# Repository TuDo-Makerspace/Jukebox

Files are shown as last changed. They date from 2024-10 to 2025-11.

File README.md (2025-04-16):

# Jukebox

This repository contains everything related to our sacred Jukebox. For more information, please refer to one of the following sections:

- [Usage](https://tudo-makerspace.github.io/Jukebox/Docs/Usage.html)
- [Hardware Documentation](https://tudo-makerspace.github.io/Jukebox/Docs/Hardware.html)
- [Software Documentation]() TODO

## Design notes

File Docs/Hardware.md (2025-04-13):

# Hardware

## Jukebox

The original jukebox used in our project is an [NSM Satellite 200](https://www.jukebox-world.de/Forum/Archiv/NSM/NSMSatellite200.htm), likely produced sometime in the late 1980s.

In this document we will only cover the hardware modifications made for our project. For detailed information on the jukebox's original hardware and specifications, please consult the following resources:

- [NSM Satellite 200 on Jukebox-World.de](https://www.jukebox-world.de/Forum/Archiv/NSM/NSMSatellite200.htm)
- [NSM Satellite 200 at Propstore Auction](https://propstoreauction.com/lot-details/index/catalog/359/lot/119259)
- [NSM Jukebox Image Archive on Jukebox-World.de](https://www.jukebox-world.de/Forum/Archiv/NSM/NSM-Bilder-Uebersicht.htm)

## Modifications

Most original components of the jukebox were removed and replaced with modern hardware. The primary modifications include:

- Logic and Playback: The primary logic and audio playback are now managed by a Raspberry Pi. *(TODO: Specify Raspberry Pi model)*
- Speakers: The Original speakers have been replaced. *(TODO: Document exact speaker model/specifications)*
- Audio Processing and Amplification: Audio output is managed by a [WONDOM APM2 DSP Board](https://store.sure-electronics.com/product/AA-AP23122) in combination with two amplifier boards. *(TODO: Specify amplifier board models)*
- Volume Control: The volume adjustment buttons located at the back of the jukebox are directly wired to the DSP board.
- Lighting: The original lighting controller was replaced by a custom lamp driver board which can be driven directly from the Raspberry Pi.
- Keypad Interface: A custom keypad decoder circuit was developed, allowing the Raspberry Pi to interpret user input from the original jukebox keypad.

### Power Supply

The jukebox utilizes two 12V power supplies and two 5V USB adapters to power its components:

- Audio Components: One low-noise 12V power supply provides clean, stable power specifically for audio components.
- Lamps: A separate 12V power supply independently powers the lamps.
- RPi and DSP Board: Two dedicated 5V USB adapters supply power to the Raspberry Pi and the DSP board.

All power supplies are connected to single power strip.

*(TODO: Specify exact power supply models/ratings)*

## Components

The following picture highlights all the components built into the jukebox:

TODO Add picture

Here's the respective block diagram:

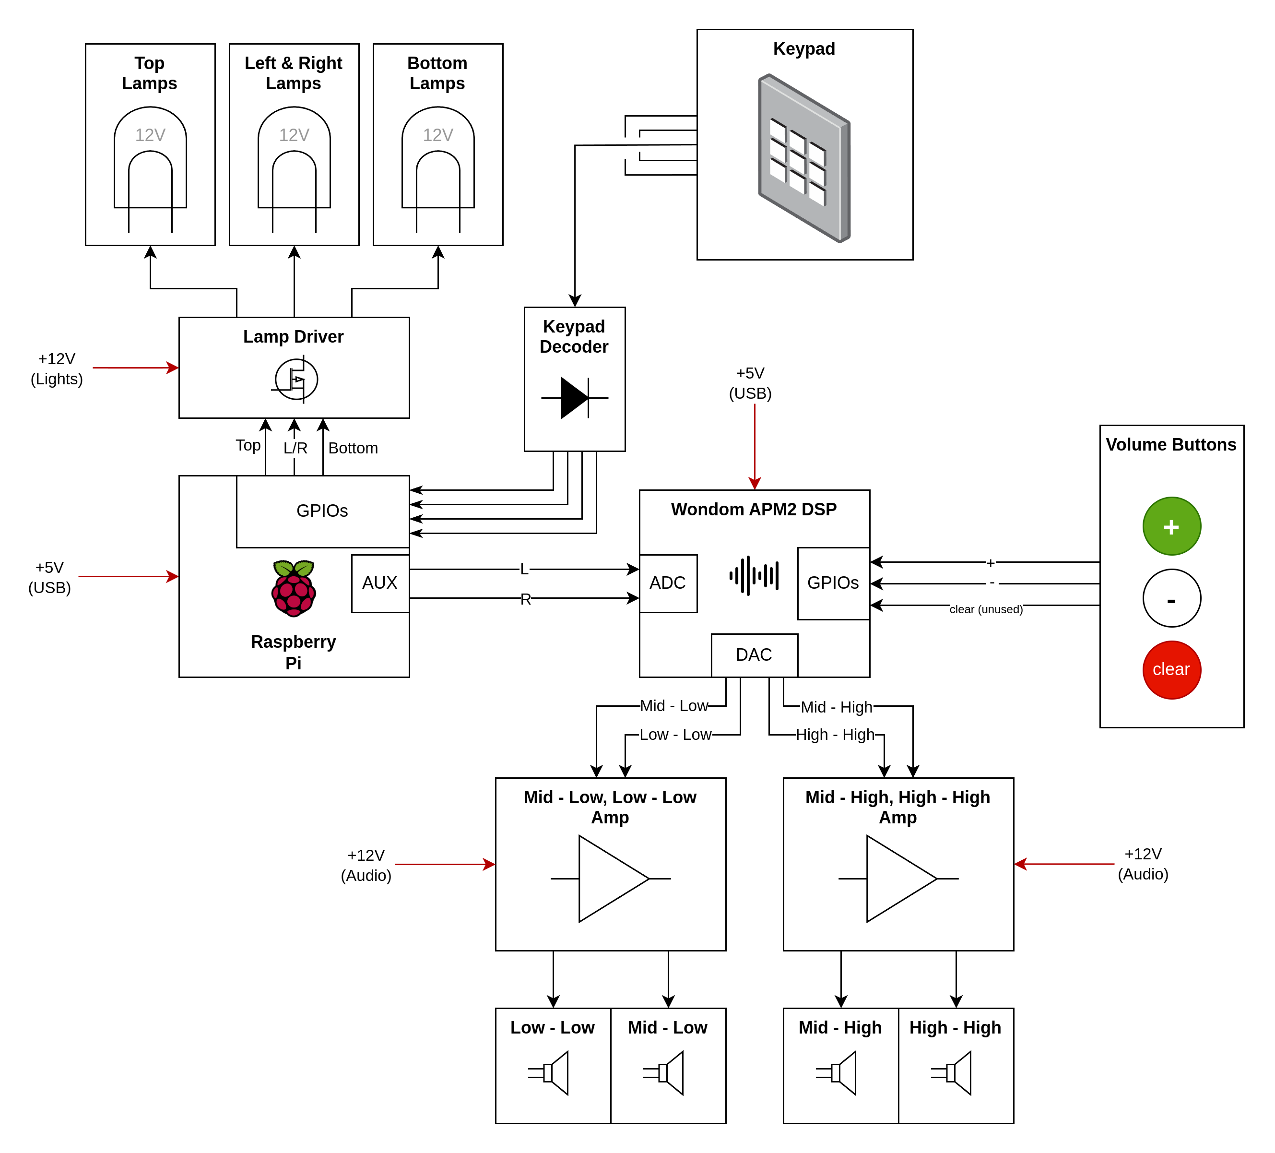
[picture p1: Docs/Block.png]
Block Diagram


### Raspberry Pi

The Raspberry Pi serves as the primary control unit for the jukebox, managing all logical operations and handling song playback. Detailed information about the software running on the Pi can be found in the [software documentation](https://tudo-makerspace.github.io/Jukebox/Docs/Software.html).

To interface with other components, a custom perfboard has been created, which plugs directly into the Raspberry Pi's GPIO pins. This perfboard provides connections to the lamp driver. It also contains the keypad decoder circuit (refer to the Keypad section for more details) along with a connection to the Keypad PCB itself.

Audio output from the Raspberry Pi is routed via its built-in 3.5mm audio jack, which connects directly to the DSP board. Initially, an attempt was made to utilize the I²S interface for improved audio fidelity; however, due to reliability issues arising from the Raspberry Pi's lack of a dedicated master clock, this approach was abandoned. Consequently, the perfboard contains several unused wires that were intended for I²S connections.

Power to the Raspberry Pi is supplied by a dedicated 5V USB adapter through its micro USB port.

### Lamp Driver

The jukebox uses [standard 12V T10 lamps](https://www.amazon.de/dp/B0CBKYPM57?ref_=ppx_hzsearch_conn_dt_b_fed_asin_title_1) distributed across three independently controllable segments:

- Top
- Left & Right (wired together)
- Bottom

To control these segments, a custom lamp driver board was designed to convert the Raspberry Pi’s 3.3V GPIO outputs to 12V control signals. The KiCAD design files are available [here](https://github.com/TuDo-Makerspace/Jukebox/tree/main/Lamps).

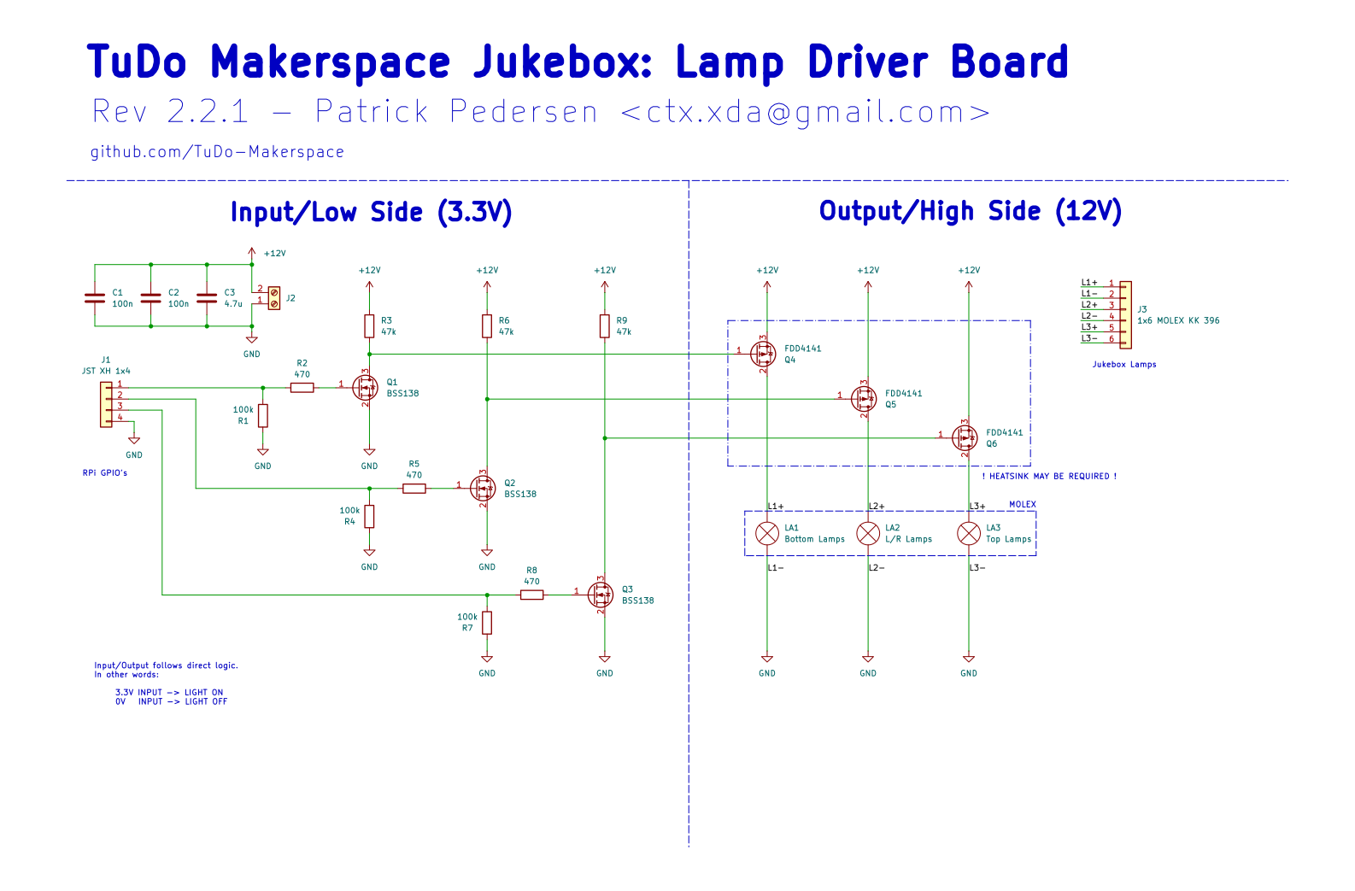
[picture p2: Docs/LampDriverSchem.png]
Lamp Driver Schematic


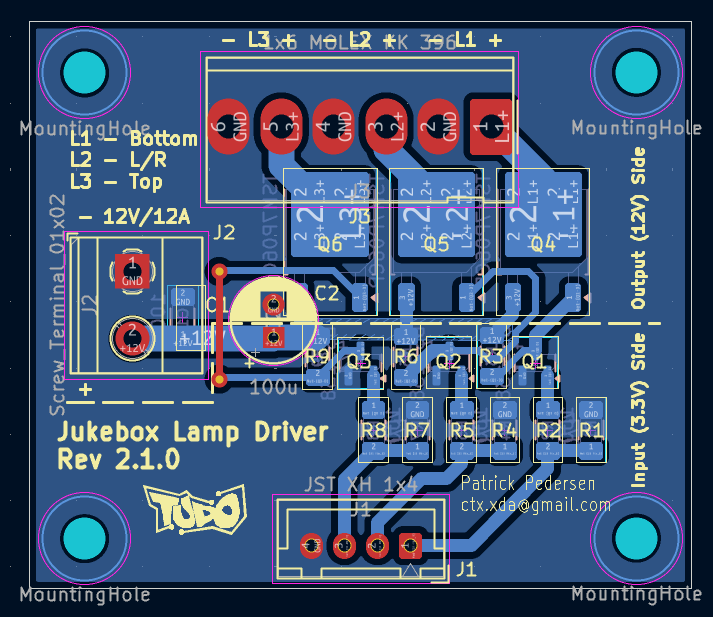
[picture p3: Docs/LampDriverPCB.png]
Lamp Driver PCB


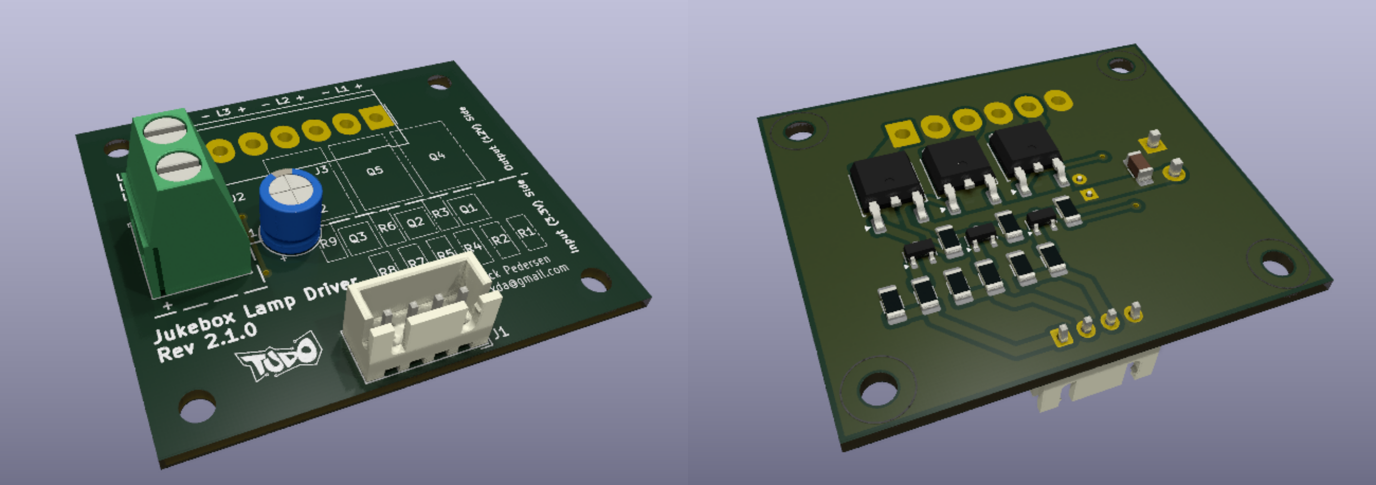
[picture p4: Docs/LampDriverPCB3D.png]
Lamp Driver PCB 3D


The lamp driver receives 12V power from the lighting power supply and connects to the Raspberry Pi via a 4-pin JST connector carrying `GND`, `Top`, `L/R`, and `Bottom` signals. Lamp outputs are routed through a 6-pin Molex connector, with each segment receiving a dedicated `+` and `-` connection. When all lamps are active, the board can draw up to 6A at 12V, with the `L/R` segment being the most power-hungry (up to 3A).

Signal amplification is handled in two stages:
1. The 3.3V GPIO signal is boosted to 12V using a BSS138 N-channel MOSFET.
2. This 12V signal is then used to switch a P-channel power MOSFET that controls the lamp segment.

In the current hardware revision, **TSM7P06CP** P-MOSFETs are used instead of the **FDD4141** parts shown in the schematic. Unfortunately, the TSM7P06CP has a significantly higher R<sub>DS(on)</sub>, which leads to heat buildup under load. Thermal testing has shown temperatures reaching up to 60°C with the current heatsink. While this remains within safe operating limits, we added a layer of Kapton tape between the heatsink and the wooden enclosure as a precaution.

**Recommendation:** For improved thermal performance, we suggest replacing the TSM7P06CP MOSFETs with FDD4141s in a future revision. This can be done either by updating the PCB layout or replacing the components on the current board.

### Keypad

TODO

### DSP

### DSP Board

The jukebox’s audio processing is handled by a [WONDOM APM2 DSP Board](https://store.sure-electronics.com/product/AA-AP23122).

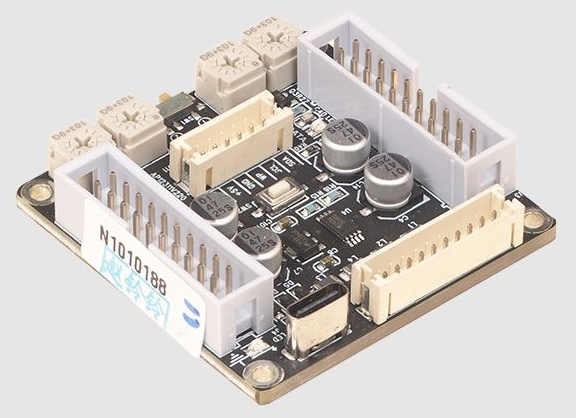
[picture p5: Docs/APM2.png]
WONDOM APM2 DSP Board


The DSP board primarily functions as a 4-way crossover, splitting the incoming audio signal into four distinct frequency bands:

- Low-Low
- Low-Mid
- High-Mid
- High-High

The board receives stereo audio input from the Raspberry Pi’s 3.5mm jack via its ADC input pins (AINL, AINR) and outputs processed audio through four DAC channels (DAC0–DAC3), which are connected to two separate amplifier boards.

The volume and clear buttons on the back of the jukebox are directly wired to the GPIO pins of the DSP board:

| Button | GPIO Pin |
| --- | --- |
| + | GPIO 10  |
| - | GPIO 11  |
| Clear  | TODO |

The volume buttons adjust the gain of the DSP, while the clear button is currently unused.

The DSP configuration is developed and uploaded using [SigmaStudio](https://www.analog.com/en/resources/evaluation-hardware-and-software/embedded-development-software/ss_sigst_02.html). The corresponding project file is available [here](https://github.com/TuDo-Makerspace/Jukebox/tree/main/Sound/DSP).

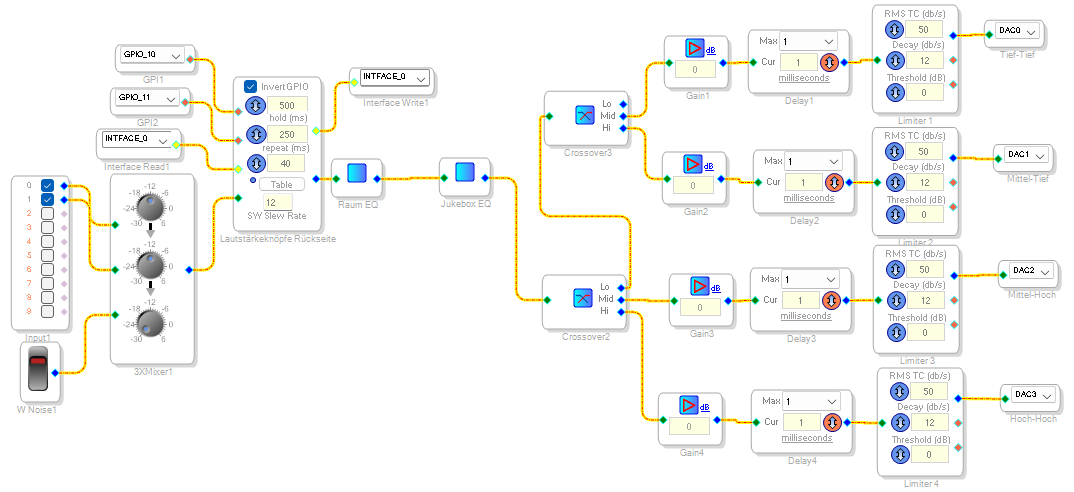
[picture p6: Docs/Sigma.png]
Sigma Studio


A dedicated USB programming board is used to upload the SigmaStudio configuration. It can be found inside the jukebox.

Further documentation and details about the DSP board, as well as how to program it, can be found in [this manual](https://files.sure-electronics.com/download/The_correspondence_of_APM2_hardware_and_DSP_program.pdf). [Video tutorials](https://www.youtube.com/watch?v=TjN1SGKeVvw) are also available.

#### Troubleshooting Tips

Here are some common frustrations we encountered while working with the DSP board:

- **USB not recognized (usb device highlighted red):**
    - Power off the DSP board and unplug the programmer
    - Unplug the programmer's USB cable
    - Replug the programmer's USB cable, check for the device to appear green in SigmaStudio
    - Plug the programmer into the DSP board
    - Power on the DSP board (That being said, it should already be powered on through the programmer at this point)

- **EEPROM programming stuck at "Start Download":**
    - Click *Link Project*
    - Click *Link Compile Connect*
    - Finally, click *Link Compile Download*
    - Try flashing the EEPROM again

#### Future Plans

We plan to measure the frequency response of the speakers to implement a tailored equalizer using the DSP board.

### Amplifier Boards

TODO

### Speakers

TODO

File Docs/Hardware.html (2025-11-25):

# Jukebox Hardware Docs

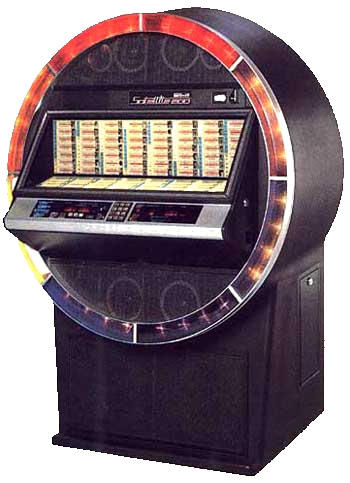
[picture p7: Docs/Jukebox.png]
Jukebox


## Jukebox

The original jukebox used in our project is an NSM Satellite 200 (https://www.jukebox-world.de/Forum/Archiv/NSM/NSMSatellite200.htm), likely produced sometime in the late 1980s.

In this document we will only cover the hardware modifications made for our project. For detailed information on the jukebox's original hardware and specifications, please consult the following resources:

- NSM Satellite 200 on Jukebox-World.de (https://www.jukebox-world.de/Forum/Archiv/NSM/NSMSatellite200.htm)
- NSM Satellite 200 at Propstore Auction (https://propstoreauction.com/lot-details/index/catalog/359/lot/119259)
- NSM Jukebox Image Archive on Jukebox-World.de (https://www.jukebox-world.de/Forum/Archiv/NSM/NSM-Bilder-Uebersicht.htm)

## Modifications

Most original components of the jukebox were removed and replaced with modern hardware. The primary modifications include:

- Logic and Playback: The primary logic and audio playback are now managed by a Raspberry Pi 3 (Model B).
- Speakers: Some of the speakers have been replaced with new ones.
- Audio Processing and Amplification: Audio output is managed by a WONDOM APM2 DSP Board (https://store.sure-electronics.com/product/AA-AP23122) in combination with two TPA3116D2 amplifier boards.
- Volume Control: The volume adjustment buttons located at the back of the jukebox are directly wired to the DSP board.
- Lighting: The original lighting controller was replaced by a custom lamp driver board which can be driven directly from the Raspberry Pi.
- Keypad Interface: A custom keypad decoder circuit was developed, allowing the Raspberry Pi to interpret user input from the original jukebox keypad.

## Power

The jukebox utilizes two 12V power supplies and two 5V USB adapters to power its components:

- Audio Components: One low-noise 12V 5A power supply provides clean and stable power specifically for audio components.
- Lamps: A separate 12V 8.5A power supply independently powers the lamps.
- RPi and DSP Board: Two dedicated 5V USB adapters supply power to the Raspberry Pi and the DSP board.

All power supplies are connected to single power strip.

## Components

The following picture highlights all the components built into the jukebox:

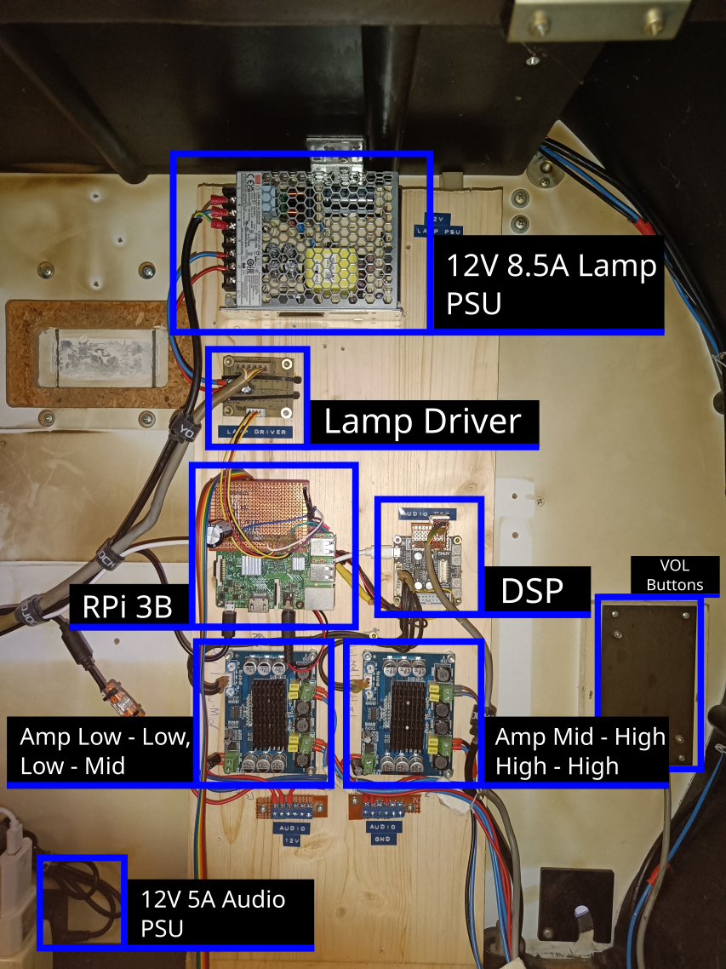
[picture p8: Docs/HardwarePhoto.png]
Picture of Hardware


Here’s the respective block diagram:

Block Diagram

## Raspberry Pi

The Raspberry Pi serves as the primary control unit for the jukebox, managing all logical operations and handling song playback. Detailed information about the software running on the Pi can be found in the software documentation (https://tudo-makerspace.github.io/Jukebox/Docs/Software.html).

To interface with other components, a custom perfboard has been created, which plugs directly into the Raspberry Pi's GPIO pins. This perfboard provides connections to the lamp driver. It also contains the keypad decoder circuit (refer to the Keypad section for more details) along with a connection to the Keypad PCB itself.

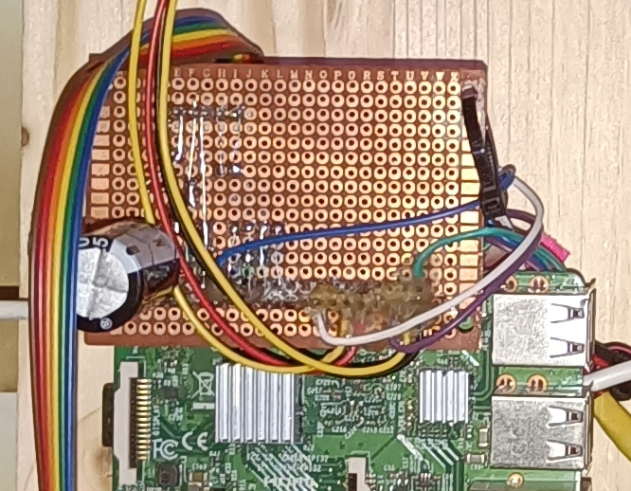
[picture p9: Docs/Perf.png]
Perfboard


Audio output from the Raspberry Pi is routed via its built-in 3.5mm audio jack, which connects directly to the DSP board. Initially, an attempt was made to utilize the I²S interface for improved audio fidelity; however, due to reliability issues arising from the Raspberry Pi's lack of a dedicated master clock, this approach was abandoned. Consequently, the perfboard contains several unused wires that were intended for I²S connections.

Power to the Raspberry Pi is supplied by a dedicated 5V USB adapter through its micro USB port.

## Lamp Driver

The jukebox uses standard 12V T10 lamps (https://www.amazon.de/dp/B0CBKYPM57?ref_=ppx_hzsearch_conn_dt_b_fed_asin_title_1) distributed across three independently controllable segments:

- Top
- Left & Right (wired together)
- Bottom

To control these segments, a custom lamp driver board was designed to convert the Raspberry Pi’s 3.3V GPIO outputs to 12V control signals. The KiCAD design files are available here (https://github.com/TuDo-Makerspace/Jukebox/tree/main/Lamps).

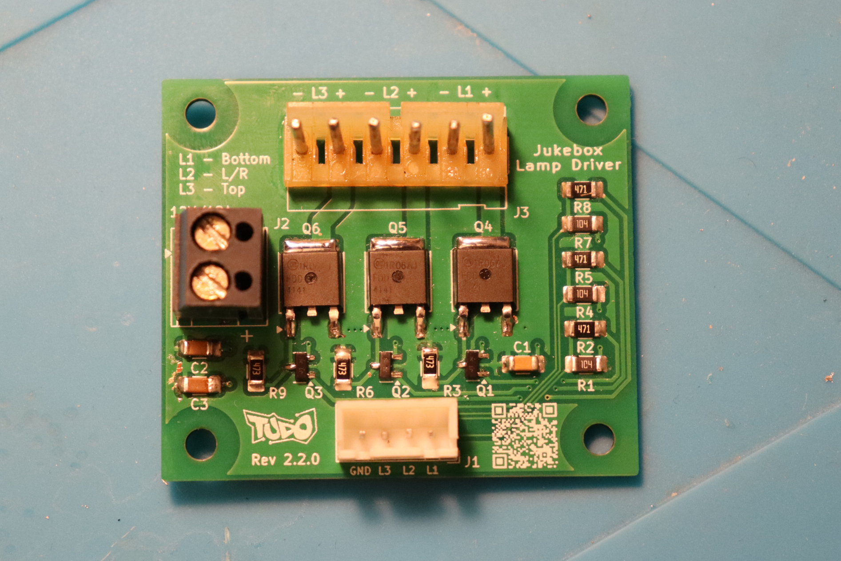
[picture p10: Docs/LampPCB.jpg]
Lamp PCB
Lamp Driver Schematic 

The lamp driver receives 12V power from the lighting power supply and connects to the Raspberry Pi via a 4-pin JST connector carrying GND, Top, L/R, and Bottom signals. Lamp outputs are routed through a 6-pin Molex connector, with each segment receiving a dedicated + and - connection. When all lamps are active, the board can draw up to 6A at 12V, with the L/R segment being the most power-hungry (up to 3A).

Signal amplification is handled in two stages:

1. The 3.3V GPIO signal is boosted to 12V using a BSS138 N-channel MOSFET.
2. This 12V signal is then used to switch a FDD4141 P-channel power MOSFET that controls the lamp segment.

The FDD4141 MOSFETs were selected to drive the lamps due to their low RDS(on) value (in our case less than 12.3 mΩ), which greatly reduces heat dissipation. In the previous PCB revision, TSM7P06CP P-channel MOSFETs with a much higher RDS(on) of about 180 mΩ were used, leading to significant heating during operation and ultimately causing one of the transistors to fail.

## Keypad

The jukebox features two keypads:

- Primary keypad: Contains digits 0-9, as well as an R and G key.
- Secondary keypad: Includes three buttons marked with a yellow, blue, and red dot.

The secondary keypad is physically connected to the primary keypad via a ribbon cable. Electrically, it functions as an extension of the primary keypad, and both share the same decoding logic.

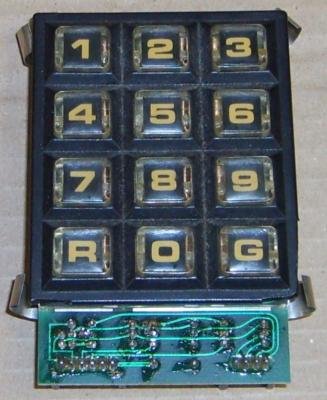
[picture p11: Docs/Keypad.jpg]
Keypad


The reverse-engineered schematic of the keypad, along with the keypad decoder that ensures Raspberry Pi-compatible logic levels, is shown below:

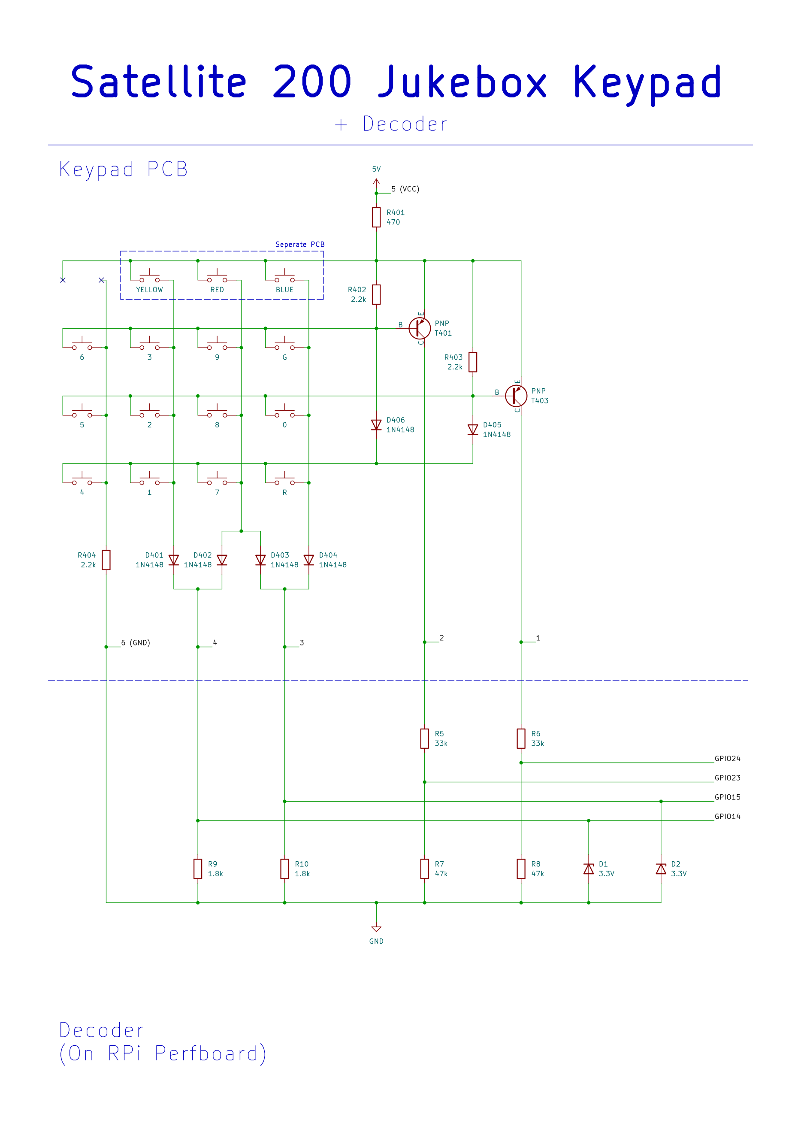
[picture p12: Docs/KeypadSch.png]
Keypad Schematic


While the keypad circuit is somewhat quirky, it boils down to providing four digital outputs whose states depend on which key is pressed. As long as only one key is pressed at a time, each key results in a unique combination of the four output lines.

The table below summarizes the output patterns and their corresponding keys:

Output Pattern (GPIO 14, GPIO 15, GPIO 23, GPIO 24) | Key
(0, 1, 0, 1) | 0
(1, 0, 1, 1) | 1
(1, 0, 0, 1) | 2
(1, 0, 1, 0) | 3
(0, 0, 1, 1) | 4
(0, 0, 0, 1) | 5
(0, 0, 1, 0) | 6
(1, 1, 1, 1) | 7
(1, 1, 0, 1) | 8
(1, 1, 1, 0) | 9
(0, 1, 1, 1) | R
(0, 1, 1, 0) | G
(1, 0, 0, 0) | YELLOW
(0, 1, 0, 0) | BLUE
(1, 1, 0, 0) | RED

To better understand how the keypad circuit functions, let's walk through a few examples:

Example 1 - Yellow Key:
Arguably the simplest case. When the yellow key is pressed, current flows through the key, diode D401, and resistor R9. This causes a voltage drop across R9, which is detected as a HIGH signal on GPIO14. In this configuration, no other current paths are active, so only GPIO14 will register a HIGH state.

Note: This example also highlights how the decoder circuit works. It simply contains resistors valued such that the measured voltage drop corresponds to the RPi's logic levels. Zener diodes are added where needed to clamp voltages safely—mainly as a safeguard if multiple keys are pressed.

Example 2 - Red Key:
Pressing the red key causes current to flow through the key, as well as diodes D402 and D403. This results in voltage drops across both R9 and R10, leading to HIGH readings on GPIO14 and GPIO15.

Example 3 - Key 3 and Transistor T401:
With this example we introduce the purpose of the PNP transistors. When no key is pressed, the base of PNP transistor T401 is pulled high via resistor R402 (2.2k), keeping the transistor turned off. Pressing key 3, however, pulls the base low through the key, D401, and R9, which switches T401 on. This allows current to flow through R6 and R8, creating voltage dividers that drop the voltage to safe 3.3V levels. As a result, both GPIO14 (via R9) and GPIO23 read HIGH.

Example 4 - Dual Transistor Activation:
When pressing any key from the bottom row of the schematic (keys 4, 1, 7, or R), both PNP transistors are activated. Their bases are connected via diodes to this row, so pressing any of these keys pulls both transistor bases low, switching them on. Consequently, for these keys, both GPIO24 and GPIO23 will always register HIGH.

## DSP Board

The jukebox’s audio processing is handled by a WONDOM APM2 DSP Board (https://store.sure-electronics.com/product/AA-AP23122).

WONDOM APM2 DSP Board

The DSP board primarily functions as a 4-way crossover, splitting the incoming audio signal into four distinct frequency bands:

- Low-Low
- Low-Mid
- High-Mid
- High-High

The board receives stereo audio input from the Raspberry Pi’s 3.5mm jack via its ADC input pins (AINL, AINR) and outputs processed audio through four DAC channels (DAC0-DAC3), which are connected to two separate amplifier boards.

The volume and clear buttons on the back of the jukebox are directly wired to the GPIO pins of the DSP board:

Button | GPIO Pin
+ | GPIO/MP 10
- | GPIO/MP 11
Clear | GPIO/MP 6

The DSP configuration is developed and uploaded using SigmaStudio (https://www.analog.com/en/resources/evaluation-hardware-and-software/embedded-development-software/ss_sigst_02.html). The corresponding project file is available here (https://github.com/TuDo-Makerspace/Jukebox/tree/main/Sound/DSP).

Sigma Studio

A dedicated USB programming board is used to upload the SigmaStudio configuration. It can be found inside the jukebox.

Further documentation and details about the DSP board, as well as how to program it, can be found in this manual (https://files.sure-electronics.com/download/The_correspondence_of_APM2_hardware_and_DSP_program.pdf). Video tutorials (https://www.youtube.com/watch?v=TjN1SGKeVvw) are also available.

### Troubleshooting Tips

Here are some common frustrations we encountered while working with the DSP board:

- USB not recognized (usb device highlighted red):
  - Power off the DSP board and unplug the programmer
  - Unplug the programmer's USB cable
  - Replug the programmer's USB cable, check for the device to appear green in SigmaStudio
  - Plug the programmer into the DSP board
  - Power on the DSP board (That being said, it should already be powered on through the programmer at this point)
- EEPROM programming stuck at "Start Download":
  - Click Link Project
  - Click Link Compile Connect
  - Click Link Compile Download
  - Try flashing the EEPROM again

### Future Plans

We plan to measure the frequency response of the speakers to implement a tailored equalizer using the DSP board.

## Amplifier Boards

The jukebox uses two HW-408 TPA3116D2 amplifier boards (https://www.amazon.de/-/en/Lazmin-TPA3116D2-Amplifier-Digital-Channels-standard/dp/B082B31GFX) to drive the speakers.

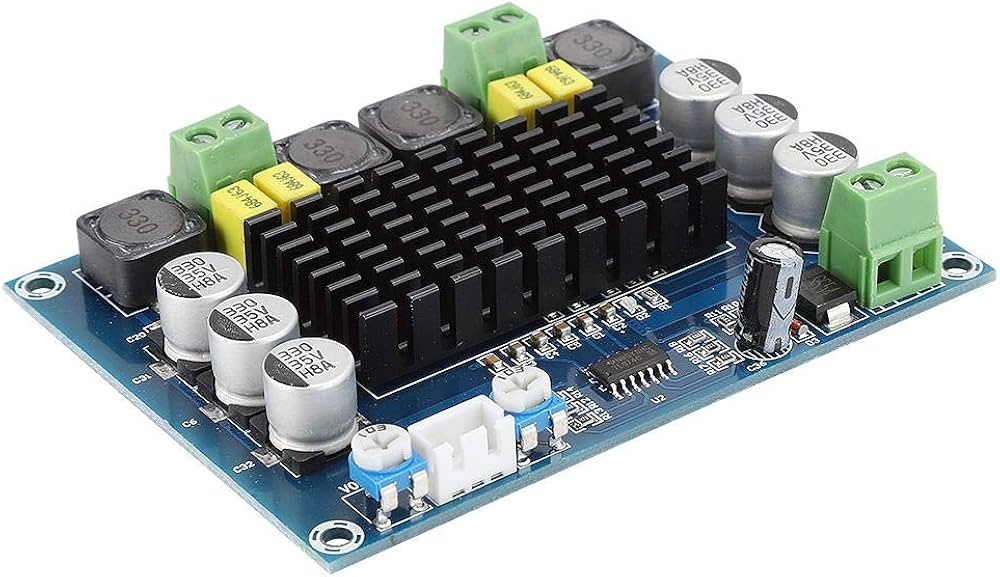
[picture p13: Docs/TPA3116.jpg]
TPA3116D2 Amplifier Board


Each board supports an input voltage range of 12V to 26V and features two output channels, each capable of delivering up to 50W. Gain for each channel can be adjusted using the small trim potentiometers on the board, however, note that these are very sensitive and should be adjusted with care.

As already mentioned in the DSP Board section, the DSP outputs four separate audio channels. These are split evenly between the two amplifier boards, with each board receiving two channels. The amplified signals are then routed to the appropriate speakers.

## Speakers

Some of the original speakers were replaced with new ones. Since we simply used speakers that were on hand at the Makerspace, their exact specifications were never documented.

We did, however, need to 3D-print an adapter to accommodate the new mid-range speakers. The 3D model is available here (https://github.com/TuDo-Makerspace/Jukebox/tree/main/Sound/Adapter).

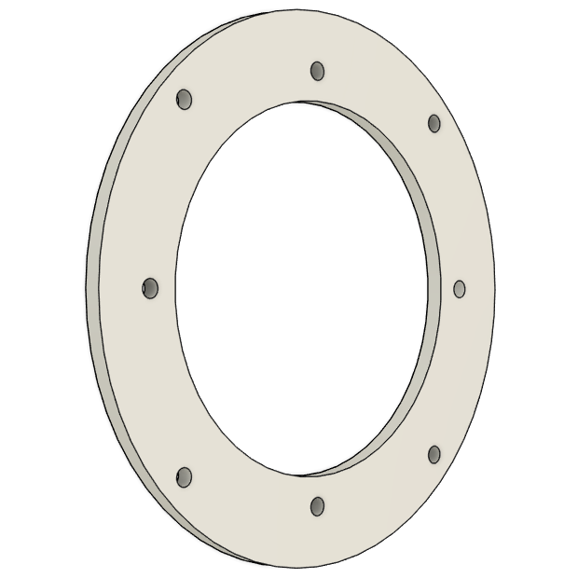
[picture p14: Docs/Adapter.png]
Speaker Adapter


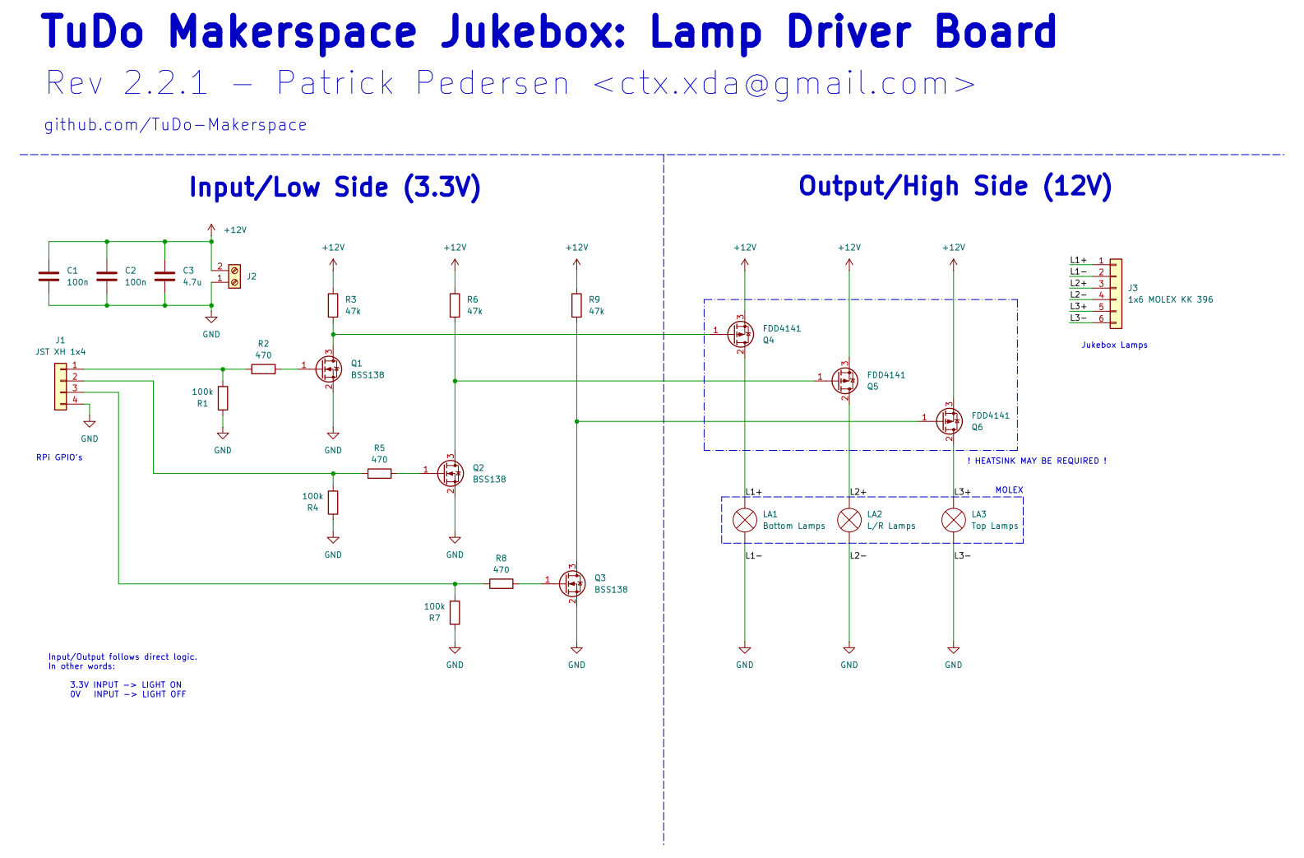
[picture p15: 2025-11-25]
Documents/dev/Jukebox/Documents/dev/Jukebox/Docs/LampDriverSchem.png

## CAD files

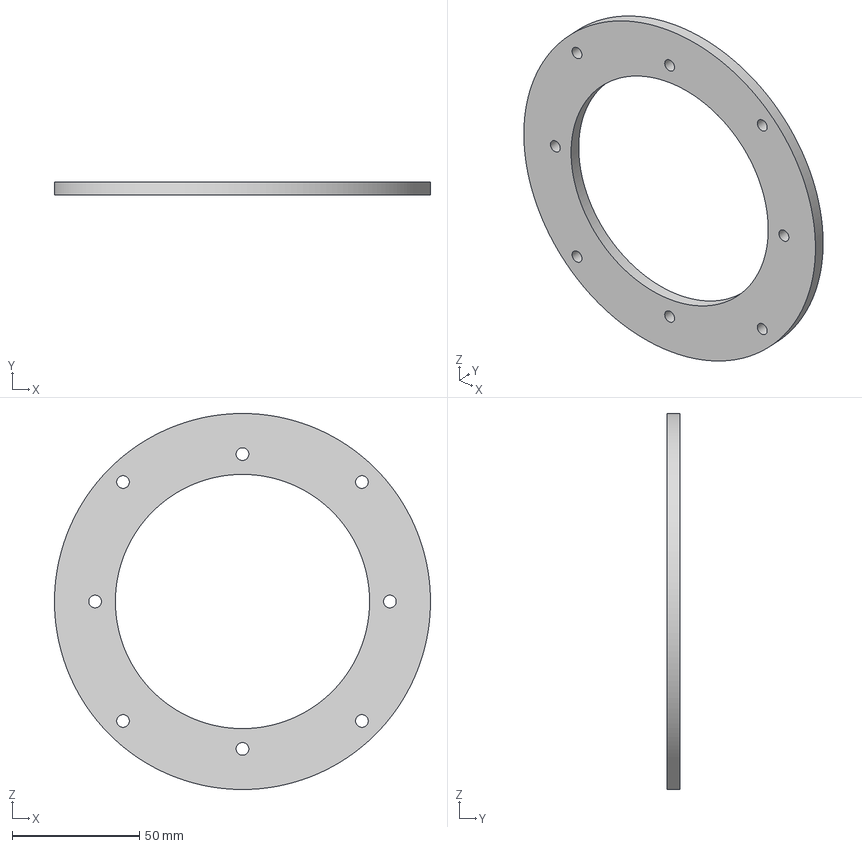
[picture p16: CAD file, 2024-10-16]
Sound/Adapter/Adapter.3mf
147.9 x 5.00 x 147.9 mm

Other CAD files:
Sound/Adapter/Adapter.f3d

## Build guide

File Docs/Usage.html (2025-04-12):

# Jukebox Usage

Jukebox

## Flowchart

Here's a high level overview of the jukebox's functionality:

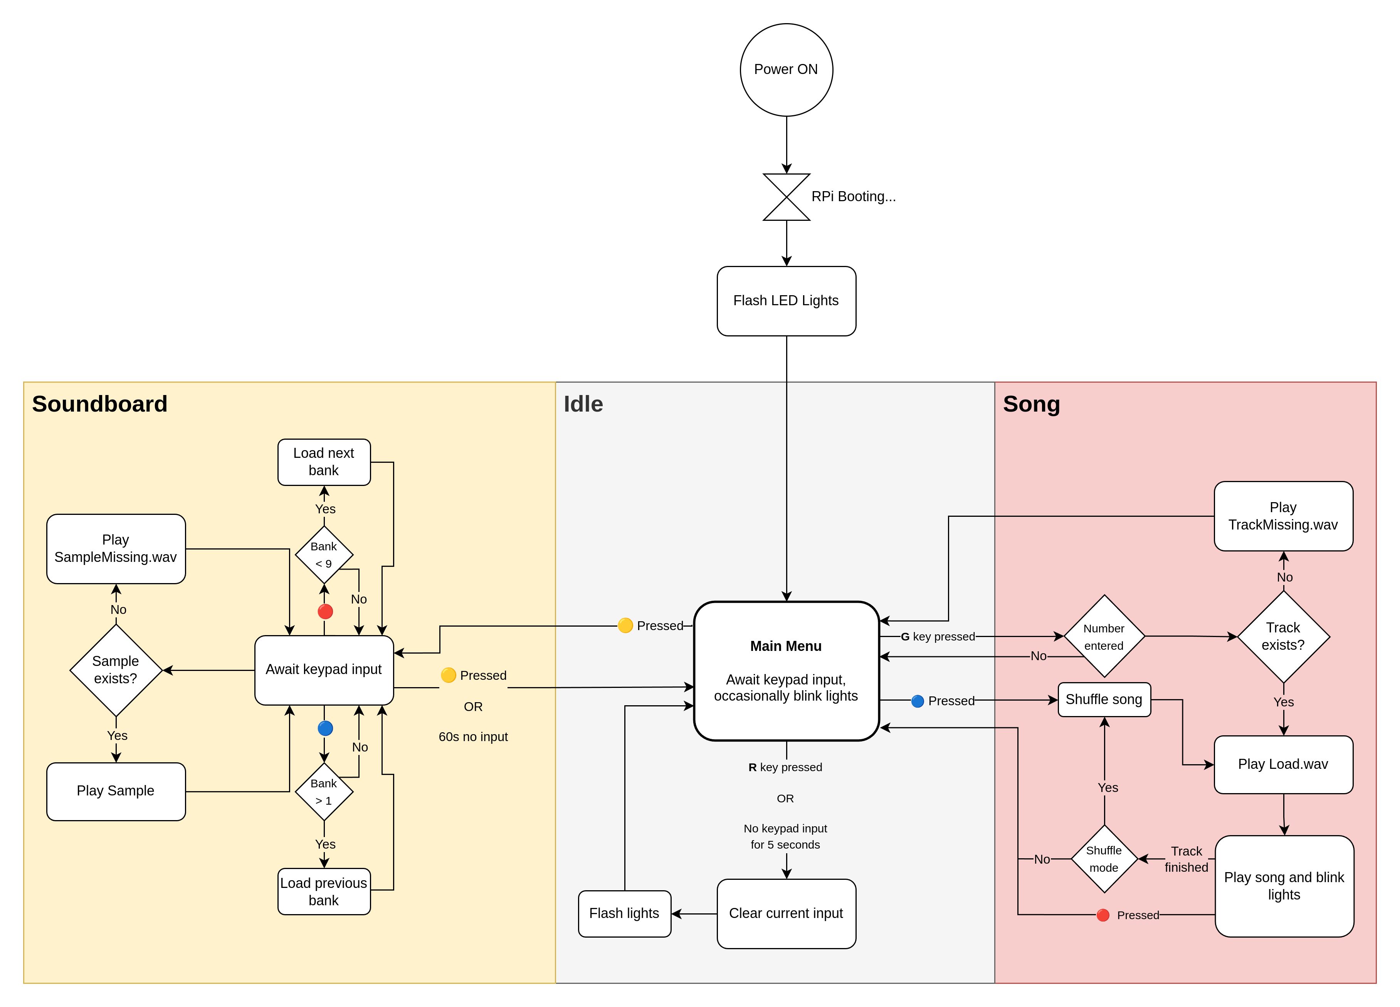
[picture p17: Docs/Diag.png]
Jukebox Flowchart


## Powering on the Jukebox

To power the jukebox on or off, flip the switch located on the power strip at the back-left side.

Note: It is normal to hear a loud "pop" sound when flipping the switch.

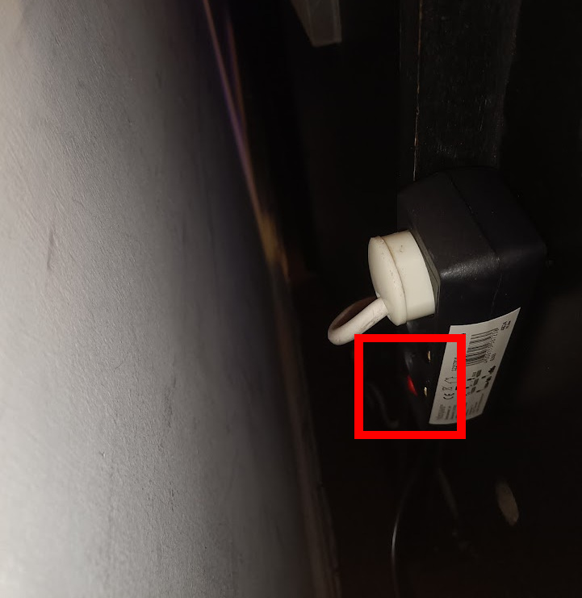
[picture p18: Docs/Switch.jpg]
Power Switch


Once powered on, the jukebox will require a short period to boot. It is ready to use when the lights begin flashing.

## Volume Control

At boot, the jukebox will start at its lowest volume. To adjust the volume, use the volume buttons located at the back-right side.

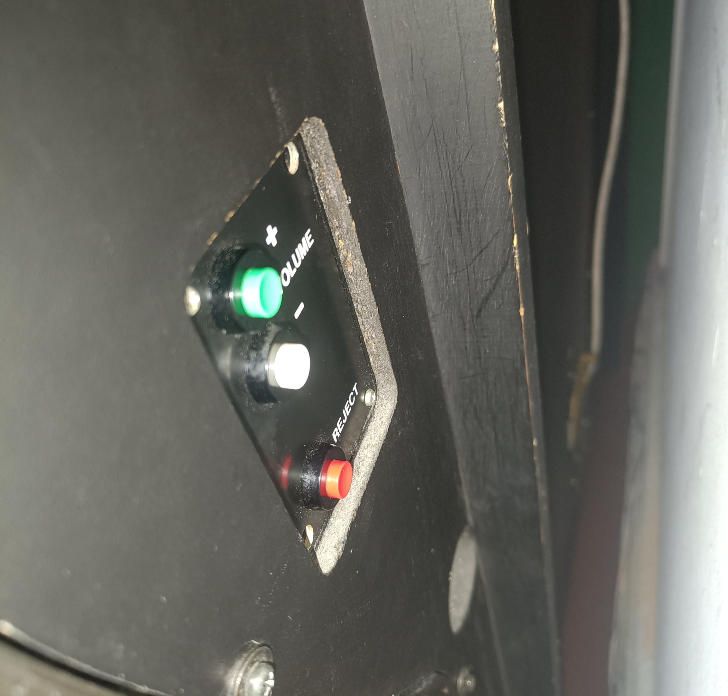
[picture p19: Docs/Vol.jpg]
Volume Control


## Selecting a Song

Enter the song number using the keypad. To confirm your selection, press the G key. The jukebox will begin playing your chosen song.

To cancel your current entry, press the R key.

Note: Your input will also automatically clear if no keys are pressed for 5 seconds.

## Shuffle

To shuffle through the songs, press the 🔵 BLUE key. The jukebox will play random songs from the library until a song is aborted (see next section).

## Aborting a Song

To stop a song currently playing, press the 🔴 RED key. This will immediately return you to the main menu.

## Soundboard Mode

To activate soundboard mode, press the 🟡 YELLOW key. In this mode, the keypad functions as a soundboard.

The jukebox has 10 soundboard banks. Upon entering soundboard mode, Bank 1 is automatically selected. Switch between banks using:

- 🔴 RED - Next bank
- 🔵 BLUE - Previous bank

To exit soundboard mode, press the 🟡 YELLOW key again. Alternatively, soundboard mode will automatically exit after 60 seconds of inactivity.

## Uploading Songs (TuDo members only)

To upload songs to the jukebox:

1. Ensure the jukebox is powered on
2. Connect to the TuDo WiFi
3. Open jukebox.local in your web browser
4. Select your desired track number
5. Upload your song either via file or URL (YouTube, Spotify, SoundCloud etc.)

## Adding Samples

This shall remain a secret ;)

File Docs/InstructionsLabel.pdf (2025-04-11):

tudo-makerspace.github.io/Jukebox/Docs/Usage.html

# Instructions /Anleitung

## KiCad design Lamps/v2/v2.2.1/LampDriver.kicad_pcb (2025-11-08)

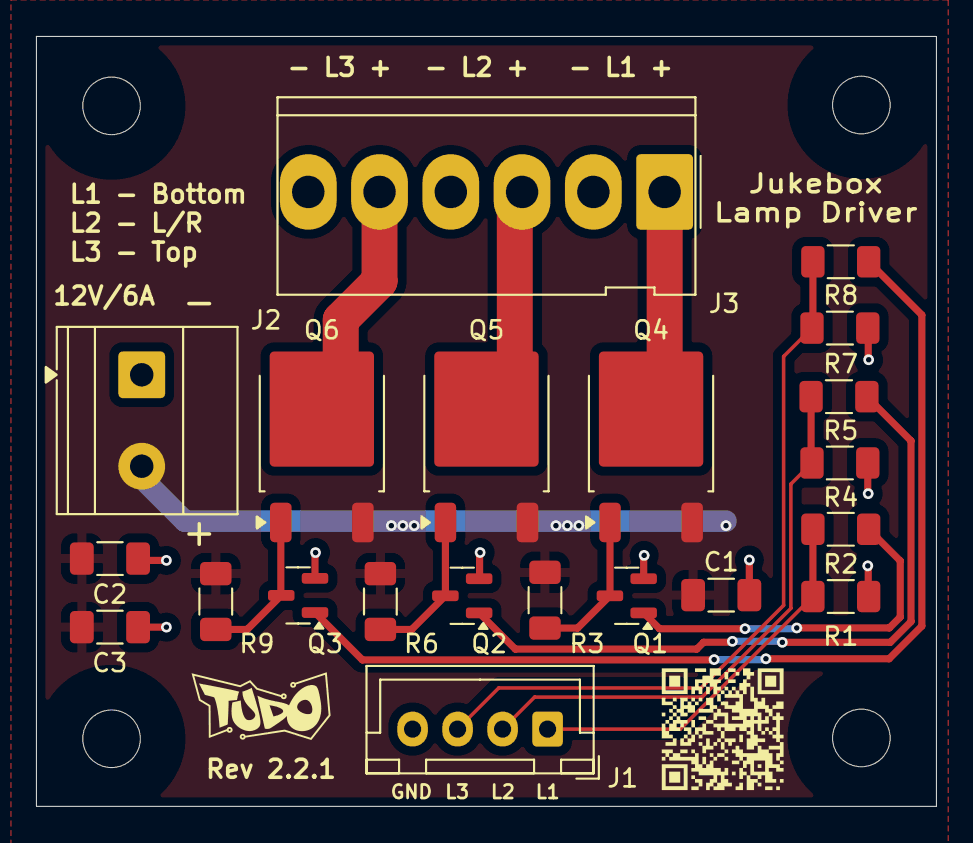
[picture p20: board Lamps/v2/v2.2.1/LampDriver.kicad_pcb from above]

Board: 2 copper layers, 50.0 x 42.8 mm, 25 parts (0 on the bottom side), 14 nets.

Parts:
C1, C2: 100n; C_1206_3216Metric_Pad1.33x1.80mm_HandSolder
C3: 4.7u; C_1206_3216Metric_Pad1.33x1.80mm_HandSolder
H1, H2, H3, H4: MountingHole; MountingHole_3.2mm_M3
J1: JST XH 1x4; JST_XH_B4B-XH-A_1x04_P2.50mm_Vertical
J2: Screw_Terminal_01x02; TerminalBlock_Phoenix_MKDS-1,5-2-5.08_1x02_P5.08mm_Horizont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
J3: 1x6 MOLEX KK 396; Molex_KK-396_5273-06A_1x06_P3.96mm_Vertical
Q1, Q2, Q3: BSS138; SOT-23
Q4, Q5, Q6: FDD4141; TO-252-2
R1, R4, R7: 100k; R_1206_3216Metric_Pad1.30x1.75mm_HandSolder
R2, R5, R8: 470; R_1206_3216Metric_Pad1.30x1.75mm_HandSolder
R3, R6, R9: 47k; R_1206_3216Metric_Pad1.30x1.75mm_HandSolder

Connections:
+12V: C1.1, C2.1, C3.1, J2.2, Q4.3 (S), Q5.3 (S), Q6.3 (S), R3.1, R6.1, R9.1
/L1+: J3.1, Q4.2 (D)
/L2+: J3.3, Q5.2 (D)
/L3+: J3.5, Q6.2 (D)
GND: C1.2, C2.2, C3.2, J1.4, J2.1, J3.2, J3.4, J3.6, Q1.2 (S), Q2.2 (S), Q3.2 (S), R1.2, R4.2, R7.2
unnamed: J1.1, R1.1, R2.2
unnamed: J1.2, R4.1, R5.2
unnamed: J1.3, R7.1, R8.2
unnamed: Q1.3 (D), Q4.1 (G), R3.2
unnamed: Q1.1 (G), R2.1
unnamed: Q2.3 (D), Q5.1 (G), R6.2
unnamed: Q2.1 (G), R5.1
unnamed: Q3.3 (D), Q6.1 (G), R9.2
unnamed: Q3.1 (G), R8.1

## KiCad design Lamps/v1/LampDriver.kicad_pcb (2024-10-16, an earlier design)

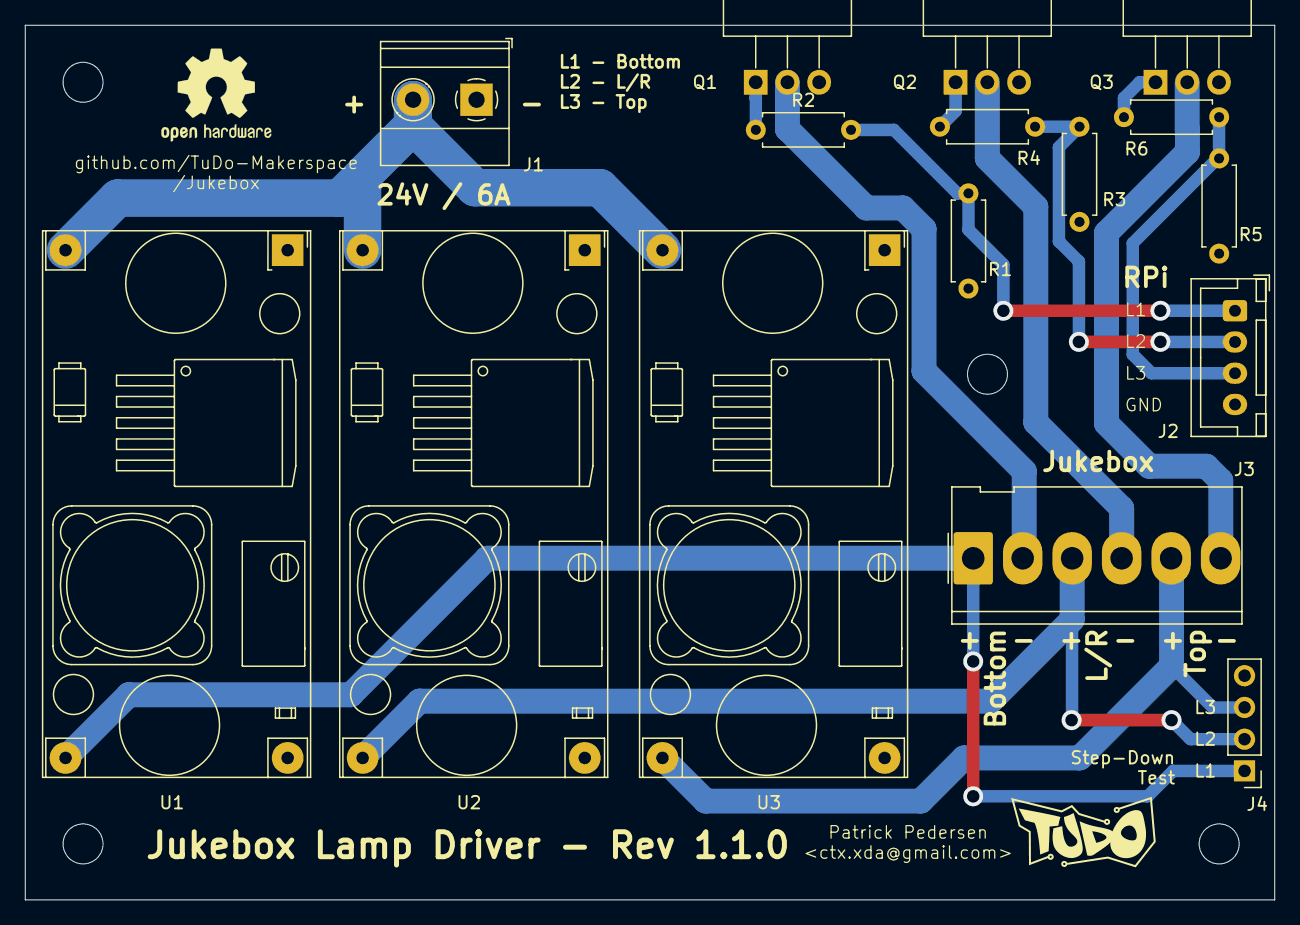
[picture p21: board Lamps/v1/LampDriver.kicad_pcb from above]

Board: 2 copper layers, 100.0 x 70.0 mm, 20 parts (0 on the bottom side), 14 nets.

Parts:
H1, H2, H3, H4: MountingHole; MountingHole_3.2mm_M3
J1: Screw_Terminal_01x02; TerminalBlock_Phoenix_MKDS-1,5-2-5.08_1x02_P5.08mm_Horizont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
J2: JST XH 1x4; JST_XH_B4B-XH-A_1x04_P2.50mm_Vertical
J3: Conn_01x06; Molex_KK-396_5273-06A_1x06_P3.96mm_Vertical
J4: Conn_01x04; PinHeader_1x04_P2.54mm_Vertical
Q1, Q2, Q3: IRFZ44N; TO-220-3_Horizontal_TabDown
R1, R3, R5: 100k; R_Axial_DIN0207_L6.3mm_D2.5mm_P7.62mm_Horizontal
R2, R4, R6: 470; R_Axial_DIN0207_L6.3mm_D2.5mm_P7.62mm_Horizontal
U1, U2, U3: DCDC_StepDown_LM2596; YAAJ_DCDC_StepDown_LM2596_Foxed

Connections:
+24V: J1.2, U1.1 (Vin), U2.1 (Vin), U3.1 (Vin)
/L1+: J3.1, J4.1, U1.4 (Vout)
/L1-: J3.2, Q1.2 (D)
/L2+: J3.3, J4.2, U2.4 (Vout)
/L2-: J3.4, Q2.2 (D)
/L3+: J3.5, J4.3, U3.4 (Vout)
/L3-: J3.6, Q3.2 (D)
GND: J1.1, J2.4, J4.4, Q1.3 (S), Q2.3 (S), Q3.3 (S), R1.2, R3.2, R5.2, U1.2 (GND), U1.3 (GND), U2.2 (GND), U2.3 (GND), U3.2 (GND), U3.3 (GND)
unnamed: J2.1, R1.1, R2.2
unnamed: J2.2, R3.1, R4.2
unnamed: J2.3, R5.1, R6.2
unnamed: Q1.1 (G), R2.1
unnamed: Q2.1 (G), R4.1
unnamed: Q3.1 (G), R6.1

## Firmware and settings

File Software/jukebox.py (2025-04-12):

"""
 Copyright (C) 2024 TuDo Makerspace

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
Description: Main script to control our Jukebox

Dependencies:
    System:
    - bpm-tag: For analyzing song BPM.
    - ffplay: For playing audio files.
    - libsox-fmt-mp3: For MP3 format support.
    Pip:
    - RPi.GPIO: For GPIO control.

Contributors:
- Patrick Pedersen <ctx.xda@gmail.com>
"""

import enum
import re
import os
import glob
import time
import wave
import signal
import random
import logging
import argparse
import threading
import subprocess
import RPi.GPIO as GPIO
import numpy as np
from pathlib import Path
import sounddevice as sd

################################################################
# Globals
################################################################

# Songs directory
JUKEBOX_SONGS_PATH = os.getenv("JUKEBOX_SONGS_PATH")

# Soundboard directory
JUKEBOX_SOUNDBOARD_PATH = os.getenv("JUKEBOX_SOUNDBOARD_PATH")

# Assets directory
JUKEBOX_ASSETS_PATH = os.getenv("JUKEBOX_ASSETS_PATH")

# Asset files and their corresponding keys (S<ee samples dict below)
ASSET_FILES = {
    "TRACK_NOT_FOUND": "TrackMissing.wav",
    "LOAD": "Load.wav",
    "MISSING": "SampleMissing.wav",
    "BANK_OUT_OF_RANGE": "BankOutOfRange.wav",
    "PRESS": "Press.wav",
}

# Interval at which the idle animation is triggered
IDLE_ANIMATION_INTERVAL = 30  # seconds

# Soundboard mode timeout
SOUNDBOARD_TIMEOUT = 60  # seconds

# Maximum Bank Number
MAX_BANK_NUMBER = 9

# Logger
logger = logging.getLogger(__name__)

# Dictionary for permanent asset samples
asset_samples = {}

# Dictionary for the current bank's soundboard samples
soundboard_samples = {}

################################################################
# Lamps
################################################################

LAMP_ON = GPIO.HIGH
LAMP_OFF = GPIO.LOW

GPIO_TOP_LAMPS = 5
GPIO_LR_LAMPS = 6
GPIO_BOT_LAMPS = 26

LIGHT_PATTERN_BLINK_ALL = [
    [1, 1, 1],
    [0, 0, 0],
    [1, 1, 1],
    [0, 0, 0],
    [1, 1, 1],
    [0, 0, 0],
    [1, 1, 1],
    [0, 0, 0],
]

LIGHT_PATTERN_UP_DOWN = [
    [1, 0, 0],
    [0, 1, 0],
    [0, 0, 1],
    [0, 1, 0],
    [1, 0, 0],
    [0, 1, 0],
    [0, 0, 1],
    [0, 1, 0],
]

LIGHT_PATTERN_DOWN_UP = [
    [0, 0, 1],
    [0, 1, 0],
    [1, 0, 0],
    [0, 1, 0],
    [0, 0, 1],
    [0, 1, 0],
    [1, 0, 0],
    [0, 1, 0],
]

LIGHT_PATTERN_TB_LR = [
    [1, 0, 1],
    [0, 1, 0],
    [1, 0, 1],
    [0, 1, 0],
    [1, 0, 1],
    [0, 1, 0],
    [1, 0, 1],
    [0, 1, 0],
]

LIGHT_PATTERN_UP_DOWN_UP = [
    [1, 0, 0],
    [0, 1, 0],
    [0, 0, 1],
    [0, 1, 0],
    [1, 0, 0],
    [0, 1, 0],
    [0, 0, 1],
    [0, 1, 0],
]

TETRIS = [
    [1, 0, 0],
    [0, 1, 0],
    [0, 0, 1],
    [0, 1, 1],
    [1, 1, 1],
    [0, 0, 0],
    [1, 1, 1],
    [0, 0, 0],
]

ALL_LIGHT_PATTERNS = [
    LIGHT_PATTERN_BLINK_ALL,
    LIGHT_PATTERN_DOWN_UP,
    LIGHT_PATTERN_UP_DOWN,
    LIGHT_PATTERN_UP_DOWN_UP,
    LIGHT_PATTERN_TB_LR,
    TETRIS,
]

################################################################
# Keypad
################################################################

GPIO_KEYPAD_PINS = [14, 15, 23, 24]

KEYPAD_RELEASED = (0, 0, 0, 0)

KEYPAD_LOOKUP = {
    (0, 1, 0, 1): "0",
    (1, 0, 1, 1): "1",
    (1, 0, 0, 1): "2",
    (1, 0, 1, 0): "3",
    (0, 0, 1, 1): "4",
    (0, 0, 0, 1): "5",
    (0, 0, 1, 0): "6",
    (1, 1, 1, 1): "7",
    (1, 1, 0, 1): "8",
    (1, 1, 1, 0): "9",
    (0, 1, 1, 1): "R",  # Reset button
    (0, 1, 1, 0): "G",  # Confirm button
    (1, 0, 0, 0): "YELLOW",  # Yellow button
    (0, 1, 0, 0): "BLUE",  # Blue button
    (1, 1, 0, 0): "RED",  # Red button
}

KEYPAD_DEBOUNCE_DELAY = 0.15  # seconds

KEYPAD_TIMEOUT = 5  # seconds

KEYPAD_TAKE_SAMPLES = 10  # Number of samples to take in case for reading the keypad

################################################################
# Functions
################################################################


def clear_terminal():
    """Clear the terminal screen."""
    os.system("clear")


def init_gpios():
    """
    Initialize the GPIO pins for the keypad and lights.
    """
    logger.info("Initializing GPIO pins...")

    GPIO.setmode(GPIO.BCM)

    # Set the GPIO pins for the keypad as inputs with pull-down resistors
    for pin in GPIO_KEYPAD_PINS:
        GPIO.setup(pin, GPIO.IN, pull_up_down=GPIO.PUD_DOWN)

    # Set the GPIO pins for the lights as outputs
    GPIO.setup(GPIO_TOP_LAMPS, GPIO.OUT)
    GPIO.setup(GPIO_LR_LAMPS, GPIO.OUT)
    GPIO.setup(GPIO_BOT_LAMPS, GPIO.OUT)

    logger.info("GPIO pins initialized.")


def song_path(number):
    """
    Get the file path of the song based on the input number.

    Args:
        number (int): The song number.

    Returns:
        str: Path to the song file, or None if no match is found.
    """
    songs_path = Path(JUKEBOX_SONGS_PATH)
    song_pattern = f"{number}_*.mp3"
    song_files = []

    for pattern in song_pattern.split():
        song_files.extend(glob.glob(str(songs_path / pattern)))

    if len(song_files) > 1:
        logger.warning(
            f"Warning: Found multiple files for number {number}, using the first one."
        )

    return song_files[0] if song_files else None


def reserved_track_numbers():
    """
    Get a list of reserved track numbers based on the song files.

    Returns:
        list: A list of reserved track numbers.
    """
    songs_path = Path(JUKEBOX_SONGS_PATH)
    reserved_numbers = []

    for file in songs_path.glob("*.mp3"):
        match = re.match(r"(\d+)_", file.stem)
        if match:
            reserved_numbers.append(int(match.group(1)))

    return reserved_numbers


def bpm_tag(file_path):
    """
    Analyze the BPM of a song using bpm-tag.

    Note: If the song hasn't been analyzed/tagged before, this may take some time.

    Args:
        file_path (str): Path to the song file.

    Returns:
        float: The detected BPM, or a fallback value of 120 if detection fails.
    """
    result = subprocess.run(
        ["bpm-tag", file_path],
        stdout=subprocess.PIPE,
        stderr=subprocess.PIPE,
        text=True,
    )
    output = result.stdout + result.stderr
    match = re.search(r"([\d.]+) BPM", output)
    bpm = float(match.group(1)) if match else 120

    if match:
        logger.info(f"Detected BPM for {file_path}: {bpm}")
    else:
        logger.error(
            f"Failed to detect BPM for {file_path}! Using 120 BPM as fallback."
        )

    return bpm


def preload_assets():
    """
    Preload all *asset* audio files (TRACK_NOT_FOUND, LOAD, MISSING, etc.)
    into memory for faster access during playback.
    """
    global asset_samples

    logger.info("Preloading asset samples...")

    for key, filename in ASSET_FILES.items():
        asset_path = Path(JUKEBOX_ASSETS_PATH) / filename

        if asset_path.exists():
            try:
                with wave.open(str(asset_path), "rb") as wf:
                    params = {
                        "channels": wf.getnchannels(),
                        "framerate": wf.getframerate(),
                        "sampwidth": wf.getsampwidth(),
                    }

                    if params["framerate"] != 44100 and params["framerate"] != 48000:
                        logger.error(
                            f"Unsupported sample rate for asset {key}: {params['framerate']}."
                        )
                        continue

                    frames = wf.readframes(wf.getnframes())
                    audio_data = np.frombuffer(frames, dtype=np.int16)
                    if params["channels"] > 1:
                        audio_data = np.reshape(audio_data, (-1, params["channels"]))

                    asset_samples[key] = (params, audio_data)
                    logger.info(f"Preloaded asset sample {key} from {asset_path}.")
            except Exception as e:
                logger.error(
                    f"Failed to preload asset sample {key} from {asset_path}: {e}"
                )
        else:
            logger.warning(f"Asset file not found: {asset_path}")

    logger.info("All asset samples preloaded.")


def preload_soundboard_samples(bank):
    """
    Preloads all *soundboard* samples (0-9, R, G, etc.) for a specific bank.
    """
    global soundboard_samples

    logger.info(f"Preloading samples for bank {bank}...")

    set_all_lamps(LAMP_ON)

    bank_path = Path(JUKEBOX_SOUNDBOARD_PATH) / str(bank)
    if not bank_path.is_dir():
        logger.warning(f"Bank {bank} directory missing. No samples preloaded.")
        set_all_lamps(LAMP_OFF)
        return

    # Clear only the old *soundboard* samples, leave asset_samples alone
    soundboard_samples.clear()

    # Load .wav files in bank folder
    for sample_file in bank_path.glob("*.wav"):
        try:
            key_match = sample_file.stem.split("_")[0].upper()
            # We only treat digits or R/G as valid keys here
            if key_match.isdigit() or key_match in {"R", "G", "RED", "BLUE"}:
                key = key_match
            else:
                logger.warning(
                    f"Unsupported sample key in file {sample_file}. Skipping."
                )
                continue

            with wave.open(str(sample_file), "rb") as wf:
                params = {
                    "channels": wf.getnchannels(),
                    "framerate": wf.getframerate(),
                    "sampwidth": wf.getsampwidth(),
                }

                if params["framerate"] != 44100 and params["framerate"] != 48000:
                    logger.error(
                        f"Unsupported sample rate for asset {key}: {params['framerate']}."
                    )
                    continue

                frames = wf.readframes(wf.getnframes())
                audio_data = np.frombuffer(frames, dtype=np.int16)
                if params["channels"] > 1:
                    audio_data = np.reshape(audio_data, (-1, params["channels"]))

                soundboard_samples[key] = (params, audio_data)
                logger.info(f"Preloaded sample {key} from {sample_file}.")
        except Exception as e:
            logger.error(f"Failed to preload sample {sample_file}: {e}")

    set_all_lamps(LAMP_OFF)
    logger.info(f"Samples preloaded for bank {bank}.")


def play_song(song_path, blocking=True):
    """
    Play a song using ffplay in a subprocess.

    Args:
        song_path (str): Path to the song file.

    Returns:
        subprocess.Popen: The process object if successful, otherwise None.
    """
    logger.info(f"Playing: {song_path}")
    try:
        process = subprocess.Popen(["ffplay", "-nodisp", "-autoexit", song_path])
        if blocking:
            process.wait()
        return process
    except FileNotFoundError:
        logger.error("Error: 'ffplay' not found. Please install it.")
    except Exception as e:
        logger.error(f"Failed to play {song_path}: {e}")
    return None


def play_sample(key, wait=True):
    """
    Play a sample. If the sample is not found in the current
    soundboard bank, play the "MISSING" sample from the assets.
    """
    # 1) Check if it's in the current soundboard bank
    if key in soundboard_samples:
        params, audio_data = soundboard_samples[key]
    else:
        if "MISSING" in asset_samples:
            params, audio_data = asset_samples["MISSING"]
            key = "MISSING"
        else:
            logger.warning("No 'MISSING' sample in assets, skipping playback.")
            return

    logger.info(f"Playing sample key: {key}")
    try:
        sd.play(audio_data, params["framerate"])
        if wait:
            sd.wait()
    except Exception as e:
        logger.error(f"Failed to play sample {key}: {e}")


def play_asset(key, wait=True):
    """
    Play an asset sample. If the asset is not found, log a warning.
    """
    if key in asset_samples:
        params, audio_data = asset_samples[key]
    else:
        logger.warning(f"Asset sample '{key}' not found.")
        return

    logger.info(f"Playing asset sample: {key}")
    try:
        sd.play(audio_data, params["framerate"])
        if wait:
            sd.wait()
    except Exception as e:
        logger.error(f"Failed to play asset sample {key}: {e}")


def set_all_lamps(state):
    """
    Set all lamps to the specified state.

    Args:
        state (int): The state to set the lamps to (LAMP_ON or LAMP_OFF).
    """
    GPIO.output(GPIO_TOP_LAMPS, state)
    GPIO.output(GPIO_LR_LAMPS, state)
    GPIO.output(GPIO_BOT_LAMPS, state)


def show_light_pattern(pattern, bpm):
    """
    Display a light pattern synchronized with the song's BPM.

    Args:
        pattern (list): Light pattern represented as a list of frames.
        bpm (float): Beats per minute of the song.
    """
    delay = 60 / bpm  # Convert bpm to delay between steps

    for frame in pattern:
        GPIO.output(GPIO_TOP_LAMPS, LAMP_ON if frame[0] else LAMP_OFF)
        GPIO.output(GPIO_LR_LAMPS, LAMP_ON if frame[1] else LAMP_OFF)
        GPIO.output(GPIO_BOT_LAMPS, LAMP_ON if frame[2] else LAMP_OFF)
        time.sleep(delay)


def random_lights_thread(bpm, stop_event):
    """
    Runs the light pattern in a separate thread until the stop_event is set.

    Args:
        bpm (float): Beats per minute of the song.
        stop_event (threading.Event): An event to signal when to stop the thread.
    """
    logger.info("Starting random light patterns thread...")

    while not stop_event.is_set():
        pattern = random.choice(ALL_LIGHT_PATTERNS)
        bpm_multiplier = random.choice([1, 2])

        for _ in range(bpm_multiplier):
            # Avoid very long delays for low BPM
            delay = max(60 / (bpm * bpm_multiplier), 0.1)
            for frame in pattern:
                if stop_event.is_set():
                    break
                GPIO.output(GPIO_TOP_LAMPS, LAMP_ON if frame[0] else LAMP_OFF)
                GPIO.output(GPIO_LR_LAMPS, LAMP_ON if frame[1] else LAMP_OFF)
                GPIO.output(GPIO_BOT_LAMPS, LAMP_ON if frame[2] else LAMP_OFF)
                time.sleep(delay)

    logger.info("Stopped random light patterns thread...")


def read_keypad_input():
    """
    Read the current state of the keypad GPIO pins.

    Returns:
        str: The button pressed (e.g., "1", "R", "G").
    """

    if KEYPAD_TAKE_SAMPLES and KEYPAD_TAKE_SAMPLES > 1:
        samples = [
            tuple(GPIO.input(pin) for pin in GPIO_KEYPAD_PINS)
            for _ in range(KEYPAD_TAKE_SAMPLES)
        ]
        # Take the most frequent state as the current state
        read = max(set(samples), key=samples.count)
    else:
        read = tuple(GPIO.input(pin) for pin in GPIO_KEYPAD_PINS)

    if read in KEYPAD_LOOKUP:
        return KEYPAD_LOOKUP[read]

    return None


def debounce_and_await_release():
    """
    Debounce the keypad input and wait for the release of all keys.
    Also provides visual feedback by turning on all lights while waiting.
    """
    set_all_lamps(LAMP_ON)
    time.sleep(KEYPAD_DEBOUNCE_DELAY)
    while tuple(GPIO.input(pin) for pin in GPIO_KEYPAD_PINS) != KEYPAD_RELEASED:
        pass
    time.sleep(KEYPAD_DEBOUNCE_DELAY)
    set_all_lamps(LAMP_OFF)


def prompt_keypad_input():
    """
    Wait for a button press on the keypad. Once a button is pressed,
    a visual feedback is given by blinking all lights. The function
    waits for the button to be released before returning.

    Returns:
        str: The button pressed (e.g., "1", "R", "G").
    """
    timeout_in = time.time() + KEYPAD_TIMEOUT

    while True:
        # Check for timeout
        if time.time() > timeout_in:
            return None

        # Read current states of GPIO pins
        read = read_keypad_input()

        # Check if the state matches a button in the lookup table
        if read:
            logger.info(f"Keypad input: {read}")
            play_asset("PRESS", wait=False)
            debounce_and_await_release()
            return read

        # Small delay to avoid excessive CPU usage
        time.sleep(0.05)


class PlayReturn(enum.Enum):
    TRACK_NOT_FOUND = 1
    ABORTED = 2
    FINISHED = 3


def play(number):
    """
    Play a song based on the input number.

    Args:
        number (int): The song number.
    """
    logger.info(f"Searching for song with number {number}...")

    spath = song_path(number)

    if not spath:
        print(f"No song found for number {number} in {JUKEBOX_SONGS_PATH}")

        set_all_lamps(LAMP_ON)
        play_asset("TRACK_NOT_FOUND")
        set_all_lamps(LAMP_OFF)

        return PlayReturn.TRACK_NOT_FOUND

    logger.info(f"Found song: {spath}")

    set_all_lamps(LAMP_ON)

    logger.info(f"Playing load sample and analyzing BPM...")

    # Play the load sample and analyze the BPM at the same time
    load_sample_thread = threading.Thread(target=play_asset, args=("LOAD",))
    load_sample_thread.start()

    bpm = bpm_tag(spath)

    # Wait for the load sample to finish
    load_sample_thread.join()

    # Play the song
    proc = play_song(spath, blocking=False)

    # Thread to display random light patterns
    stop_event = threading.Event()
    lights_thread = threading.Thread(
        target=random_lights_thread, args=(bpm, stop_event)
    )
    lights_thread.start()

    # Do the lights and check for red button press (stop)
    aborted = False
    try:
        while proc.poll() is None:
            if read_keypad_input() == "RED":
                proc.terminate()
                logger.info("Song stopped by user.")
                aborted = True
                break
    finally:
        # Signal the light thread to stop and wait for it to finish
        stop_event.set()
        lights_thread.join()

        set_all_lamps(LAMP_OFF)

        # Debounce if abort key was pressed
        # This is a little excessive, but why not...
        if aborted:
            # User still holding the button
            if read_keypad_input() == "RED":
                debounce_and_await_release()

            # User likely released the button
            else:
                time.sleep(KEYPAD_DEBOUNCE_DELAY)

    logger.info("Done playing song.")

    if aborted:
        return PlayReturn.ABORTED
    else:
        return PlayReturn.FINISHED


def idle(start_with_animation=True):
    """
    Idle mode. Plays up-down light pattern at regular intervals.
    Exits when any key on the keypad is pressed.

    Returns:
        Pressed key to exit idle mode.
    """
    logger.info("Entering idle mode...")

    skip = not start_with_animation

    def key_pressed_check():
        """Checks if a key is pressed and handles lamp blinking for feedback."""
        key = read_keypad_input()
        if key:
            logger.info(f"Key pressed: {key}")
            play_asset("PRESS", wait=False)
            debounce_and_await_release()
        return key

    while True:
        if not skip:
            # Play light pattern animation
            for pattern in [TETRIS]:
                for frame in pattern:
                    GPIO.output(GPIO_TOP_LAMPS, LAMP_ON if frame[0] else LAMP_OFF)
                    GPIO.output(GPIO_LR_LAMPS, LAMP_ON if frame[1] else LAMP_OFF)
                    GPIO.output(GPIO_BOT_LAMPS, LAMP_ON if frame[2] else LAMP_OFF)

                    # Delay for the current frame while checking for key presses
                    frame_delay = time.time() + 0.25
                    while time.time() < frame_delay:
                        k = key_pressed_check()
                        if k:
                            logger.info("Exiting idle mode...")
                            return k

            set_all_lamps(LAMP_OFF)

        skip = False

        # Wait for the next animation trigger
        trigger_in = time.time() + IDLE_ANIMATION_INTERVAL

        # Check for key presses during idle interval
        while time.time() < trigger_in:
            k = key_pressed_check()
            if k:
                logger.info("Exiting idle mode...")
                return k
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

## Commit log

2024-10-16 Added Lamp driver board
    [LampDriver.kicad_pcb, LampDriver.kicad_sch, LampDriver_MODIFIED.kicad_sch]
2024-10-16 Added adapter for speakers
    [Adapter.3mf, Adapter.f3d]
2024-11-10 Webserver: Fixed upload buttons on phones
2024-11-12 Jukebox: Keypad mapping + Minor test arg fix
    [jukebox.py]
2024-11-12 Jukebox: Fixed keypad edgecase
    [jukebox.py]
2024-11-12 Jukebox: Play Track Not Found sample
2024-11-13 Jukebox: Added stop button + Other minor fixes
    [jukebox.py]
2024-11-14 Jukebox: Added support for random button
2024-11-14 Jukebox: Fixed wrong compare on random button
    [jukebox.py]
2024-11-14 Webserver: Limit track title in upload modal
2024-11-15 Jukebox: Minor fixes to idle mode
    [jukebox.py]
2024-11-15 Jukebox: More idle fixes
    [jukebox.py]
2024-11-17 Jukebox: Support soumdboard samples for non-numeric keys
2024-11-17 Jukebox: Soundboard: Added missing sample sound + Preload samples whenever we enter soundboard
    [jukebox.py]
2024-11-18 Webserver: Show blue and red circle emojis for blue and red button in sb
2024-11-18 Jukebox: Sample buttons for better reliability + Fixed soundboard
    [jukebox.py]
2024-11-18 Jukebox: Soundboard: Play sample on button press, not release
2024-11-20 Webserver: See commit details
    Samples:
    - Fixed deletions of samples
    - Convert non 44100 or 48000 wavs to 44100
    As well as minor code clean-up
2025-02-24 Lamps: Rev 2.0 of lamp driver board
    [LampDriver.kicad_pcb, LampDriver.kicad_sch, LampDriver_MODIFIED.kicad_sch]
2025-03-22 Jukebox: Implement sample banks
2025-03-22 Jukebox: New lights board uses active high logic
2025-03-28 Webserver: Add sample bank pages
2025-03-28 Jukebox: Return if key not found for sample
2025-03-28 Jukebox: Seperate assets and samples
2025-03-28 Webserver: Do not use red and blue keys for samples
2025-03-28 Webserver: Fix akward arrow buttons on dark mode
2025-04-10 Webserver: Trim silence at start of samples
2025-04-11 Flowchart: Minor correction
2025-04-11 Docs: Improve flowchart
2025-04-12 jukebox_webserver: Perform lufs normalization on uploaded tracks and samples
2025-04-13 First draft of hardware docs
    [LampDriver.kicad_pcb, LampDriver.kicad_sch]
2025-04-13 Keypad: Add kicad schematic
    [Keypad.kicad_pcb, Keypad.kicad_sch]
2025-04-15 Keypad: Kicad schematic completed
    [Keypad.kicad_sch]
2025-04-15 Docs: More keypad stuff
    [Keypad.kicad_sch]
2025-04-17 Docs: Hardware: Add info about clear button gpio
2025-11-06 Lamps: PCB rev 2.2.0
    [LampDriver.kicad_pcb, LampDriver.kicad_sch]
2025-11-08 Lamps: PCB: Last touches
    [LampDriver.kicad_pcb]
2025-11-08 Lamps: PCB: minor changes qualify as v2.2.1
    [LampDriver.kicad_pcb, LampDriver.kicad_sch]
2025-11-25 Docs: Update Lamp driver docs

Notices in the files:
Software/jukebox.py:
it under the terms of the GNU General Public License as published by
